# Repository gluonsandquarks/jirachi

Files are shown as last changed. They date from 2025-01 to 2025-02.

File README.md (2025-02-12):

# Jirachi: self-balancing Reuleaux triangle

Jirachi is an embedded device in the shape of a Reuleaux triangle which is able to balance itself in the positions where the system is unstable. This is done through active control in the form of a PID controller.

> [!NOTE]
> This project is still active and being worked on, the firmware for the device and the software for the control GUI is mostly done, the hardware is completely done (no plan for future revisions), and the mechanical side of the project is currently the main focus, as well as documentation.
>
> UPDATE: The mechanical design is mostly done, just need to perform more tests and tune the PID controller again for this new design, after everything's done I'll update the documentation with a nice gif and pictures :)

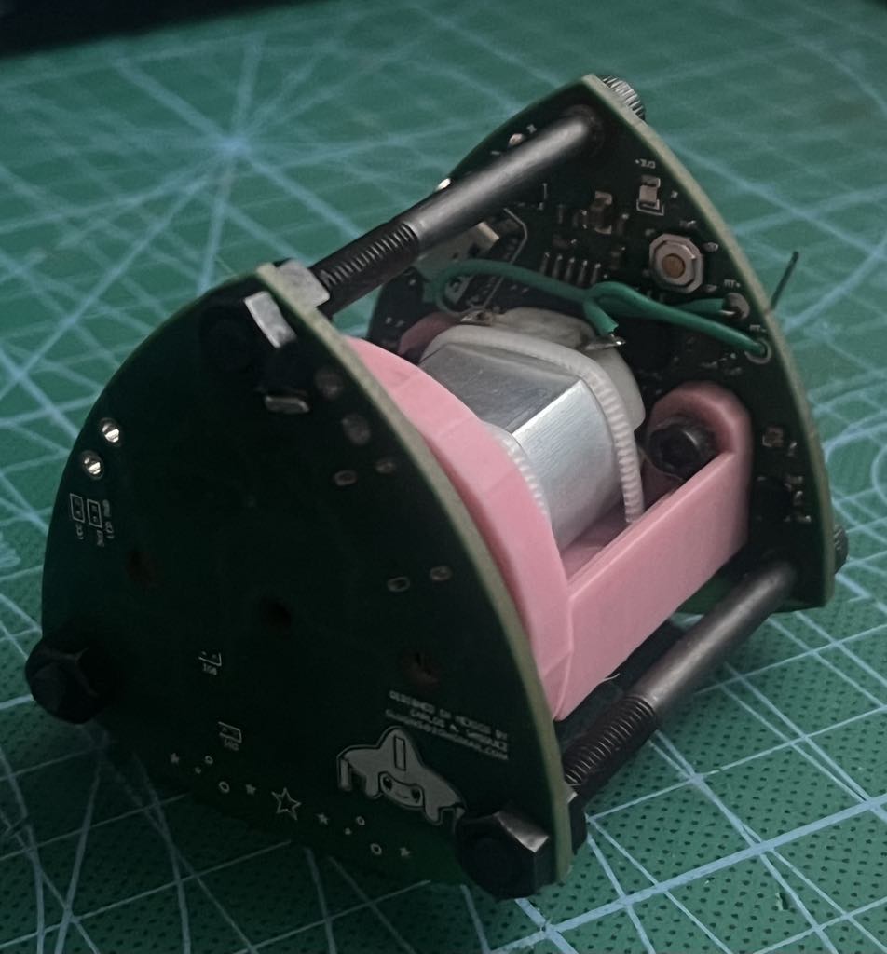
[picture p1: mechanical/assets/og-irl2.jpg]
Jirachi Device


This repository keeps track of all the work that's needed to be done in order to create a product from scratch. The solutions provided aren't necessarily the best ones out there, but the ones that made sense to me as a solo developer given the nature of the project (which is a personal project if it wasn't obvious).

## Overview

As you would be able to tell from the four directories at the root of the repository, each of them aims to solve a specific problem that would ultimately solve the "i want a balancing-robot-thingy" issue. Here's an brief explanation of each folder in the same chronology as this was being developed:

- `hardware/`: This folder holds all the files related to the electronics of the device. This is essentially the device itself and the schematic design and PCB layout was done on Altium Designer. You will be able to find each of the schematics, the PCB project, and the outputs generated by the program to manufacture and assemble the PCB. There are other miscellaneous files used by the program to correctly understand the relation between the mechanical constrains of the device and the actual electronics design needed to be done. [You can read more about this section over here.](hardware/README.md)
- `mechanical/`: This folder holds all the files and data related to the mechanical design of the device. This means any part that is not the PCB itself or soldered directly to it. Technically this aspect of the device was being developed alongside the hardware, as I was jumping back and forth between programs so I could generate mechanical data to add to the hardware program, and viceversa so I could generate a plausible assembly from the PCB data. The mechanical design was worked on CATIA V5, the most interesting thing is the Reuleaux triangle, although it is pretty trivial to implement. Other than that, here is where I defined the assembly, the shape of the motor mount, the flywheel, enclosure, etc. [You can read more about this section over here.](mechanical/README.md)
- `fimrware/`: This folder holds all the source code running on the device. The code implements the RGB LED controller, intertial measurement unit driver, motor driver, Bluetooth Low Energy driver, the PID controller and the sensor-fusion algorithm. The source code is written in C, using the ESP-IDF framework. [You can read more about this section over here.](firmware/README.md)
- `gui/`: This folder holds the source code of a GUI application used to tune the PID controller and enable the control algorithm over BLE. It's implemented in Rust just because I wanted to learn it in a more complex project hehe. It is supposed to be cross-platform but I've just tested on Windows cause my linux distro on my dual booted machine is broken at the moment so whatever (i would just use linux only but i wanted to use some specific CAD programs, so cry about it :P). [You can read more about this section over here.](gui/README.md) ALSO!!! the only reason i created a GUI app to control the device was because stupid windows couldn't connect to my device without pairing first, and to do the pairing i need to define some super specific bloated BLE characteristics so whatever i just did my own solution >:))). You can read more about that particular issue [over here.](https://github.com/espressif/esp-idf/issues/10653#issuecomment-1751914245)

## Build one yourself!!! (Bill of Materials)

If, by some weird reason, you want to build this device from scratch, then let me tell you i would love to see pictures of this lol. Send 'em my way!!! Here's a high level overview of what you'd need to build this device:

- 1 x Assembled PCB: you can just order it from JLCPCB at a pretty cheap price (~20 usd per board), everything is already done for you over at the hardware directory!!
- 1 x DC motor: I used [this one](https://www.amazon.com/dp/B07JYM8H18)
- 1 x Motor coupler: I used [this one](https://www.amazon.com/dp/B0BZS347G5)
- 1 x 3D prints of the models under the [`mechanical/outputs/`](mechanical/outputs/) folder
- 3 x M4x50mm screws
- 6 x M4 nuts
- 2 x M3x10mm screws
- 2 x M3 nuts
- 1 x Li-Ion/LiPo Battery (can be any kind as long as voltage is between 5 and 3.6V, an it can deliver ~1.5A). I used a 18650 cell with a capacity of 2600 mAh
- 2 x zip ties ~2 or 3 mm in width
- 1 x sick soldering and assembly skillz

## Repository Structure
```
├───firmware   -> actual code running on the embedded device
│   ├───docs   -> extra documentation regarding algorithms
│   ├───main   -> source code, built with the esp-idf framework
│   └───tests
├───gui        -> cross-platform gui to connect and control the device
│   ├───assets -> images used by the gui README.md
│   └───src    -> rust source code
├───hardware   -> altium designer files with the schematics and PCB
│   ├───assets -> images used by the hardware README.md
│   ├───libraries -> component libraries
│   │   ├───Phil's Lab
│   │   └───Terreneitor
│   └───Project Outputs for Lucido -> gerbers, BOM and CPL files for manufactury/assembly of the boards
└───mechanical -> 3D models/designs for everything else, done in CATIA
    └───assets -> images used by the mechanical README.md
```

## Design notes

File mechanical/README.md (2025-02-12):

# Jirachi Mechanical Design
The mechanical design for the Jirachi device encloses the PCB in such a way that it extends the shape of the PCB, modifying its mechanical properties so that the control of the device is more stable.

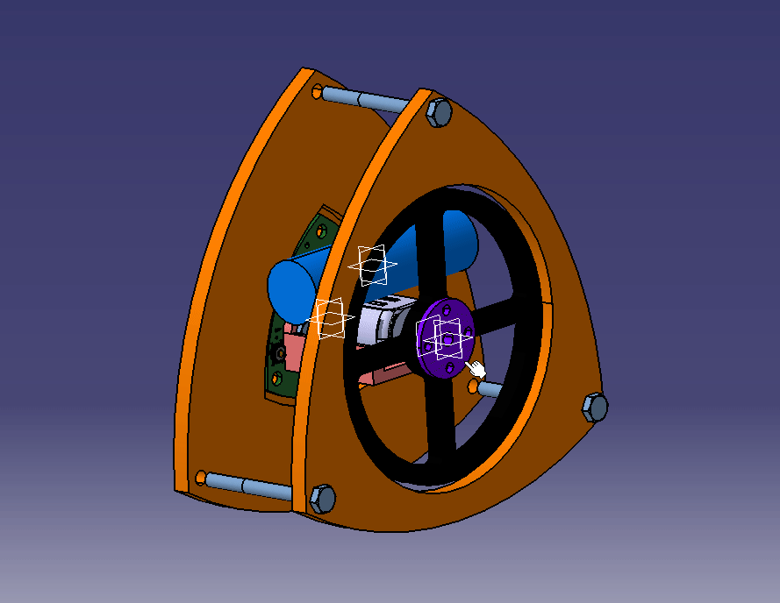
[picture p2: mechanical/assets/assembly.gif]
Assembly


The flywheel is embedded into the device and cuts some of the front plate, this is to both minimize the weight of the device as a whole and because it looks cool lol. The only thing missing is a battery holder, but i got lazy and decided to duct tape the battery on top of the motor or below the motor base (the latter sounds more secure so yeah).

The filenames of of the CATIA models are all fucked because CATIA sucks at renaming the actual archives, the links and everything will break if you try to do that so I'm just avoiding it hehe. If you open the main file `ASSYFinal.CATProduct` you will find the tree and everything should be properly named with names that actually make sense.

At the moment I still need to take pictures of the IRL assembly, but the design as a whole might be done for good.

## Original Design
The original design was implemented by trying to have the PCBs themselves be the mechanical feature that was in constant control. The following gif visualizes the original concept:

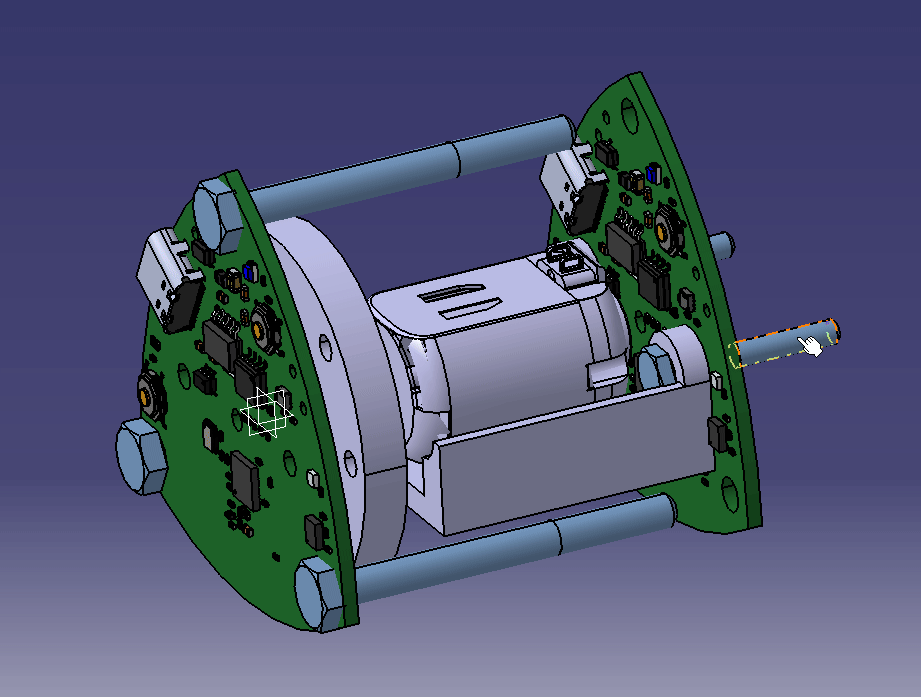
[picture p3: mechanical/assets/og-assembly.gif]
Original Assembly


As you can see, the idea was to have a PCB on one side and another on the other side, sandwiching the motor and the flywheel for the active controller to change the angular momentum of the device in such a way that it could balance itself in one of the three unstable points of the shape (the 3 vertices of the triangle). This ideally works, however after testing and after trying to tune the PID controller, it was noted that the system was really unstable due to the distribution of the moments of intertia, mass, etc.

This is analog to trying to balance a pencil in the tip of your fingers vs. trying to balance a broom in the palm of your hand. The pencil requires a way more responsive controller than the broom. In fact due to how the moments of intertia and mass are distributed on the broom, it is really easy to balance it with minimal input from your hand.

Here are some pics from the original assembly!!
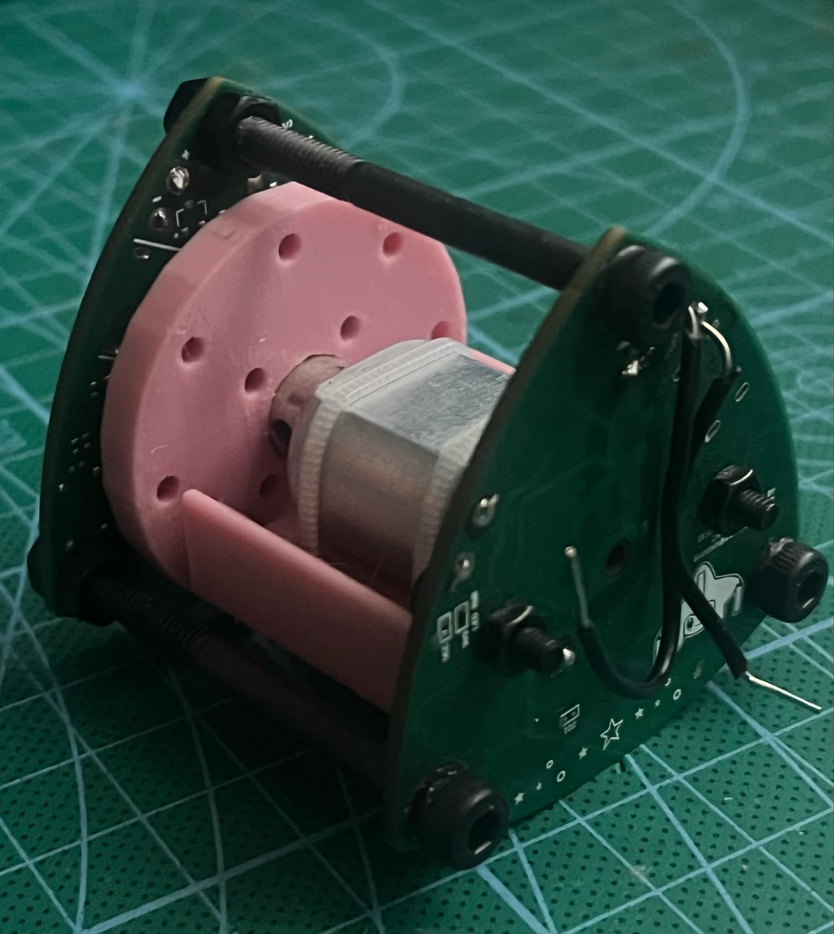
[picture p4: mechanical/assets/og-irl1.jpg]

IRL assembly

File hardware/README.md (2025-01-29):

# Jirachi Hardware

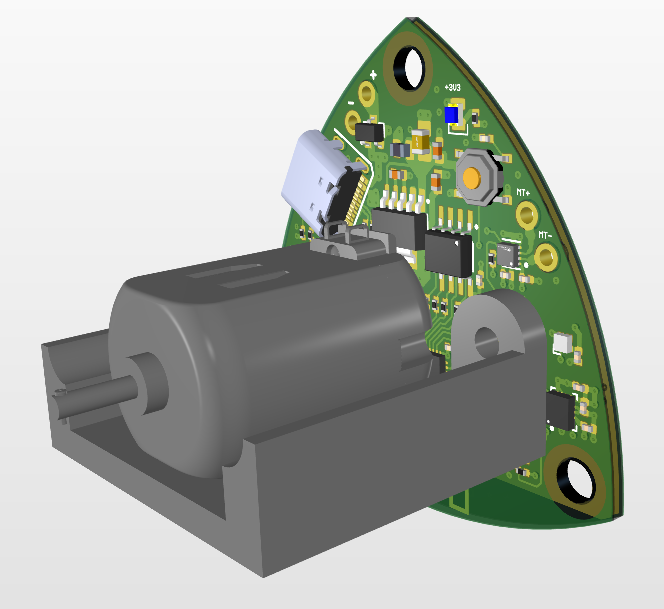
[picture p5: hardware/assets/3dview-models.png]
PCB Isometric View


The hardware for the Jirachi device is a custom designed PCB in the shape of a Reuleaux triangle. The original idea behind this design choice was to have two sets of PCBs sandwich an actuator, this way the PCB itself was designed to be the enclosure itself. Long story short, this original design didn't work [and you can read more about it over here.](../mechanical/README.md#original-design) Over all the mechanical features of the PCB didn't interfere with functionality so it stayed as it was originally planned.

The project was called `Lucido` before I decided to call it `Jirachi`, so that's why the hardware files have different filenames instead of the repository's name.

## Techincal Details

The PCB is a 4-layer board in the shape of a Reuleaux triangle. This special shape is known as a constant-width solid. The maximum width of the PCB is 50mm (you already know this size was intentional due to the discount over at JLCPCB for 4-layer boards nyehehehe, i'm poor like that :P). Here's the breakdown:

- 4-layer PCB: top and bottom layers used for signal and power routing, inner layers used exclusively as ground planes for optimal EMI and EMC.
- 50 mm max width.
- [ESP32-C3](https://www.espressif.com/sites/default/files/documentation/esp32-c3_datasheet_en.pdf): pretty cheap and powerful, able to run control algorithms smoothly, controlled through Bluetooh Low Energy.
- USB-C: This board uses the native USB/JTAG controller to program, debug and power the device. There's no fancy USB-C power delivery or anything like that, but I prefer using it over the more traditional type B and A because the current limit is a little higher ~1A.
- [W25Q128JVSIQ](https://www.winbond.com/resource-files/w25q128jv%20revf%2003272018%20plus.pdf) 128Mbit QSPI Flash.
- [TPS73733DCQR](https://www.ti.com/lit/ds/symlink/tps737.pdf) 1A low-dropout voltage regulator: this thing is a beauty thanks to the super low-dropout voltage and the max current draw available. With this IC, it was a no-brainer having the board being powered by USB or by an external single cell lithium battery.
- [ICM-42688-P](https://product.tdk.com/system/files/dam/doc/product/sensor/mortion-inertial/imu/data_sheet/ds-000347-icm-42688-p-v1.6.pdf) intertial measurment unit: it has a 3-axis accelerometer and a 3-axis gyroscope, with this it is possible to implement attitude estimation through a sensor-fusion algorithm.
- [SK6805-EC15](https://cdn-shop.adafruit.com/product-files/4492/Datasheet.pdf): you already know we need some RGB in this mf. It's just a single RGB LED onboard, but it does more than enough to signal the different states of the device.
- [DRV8837DSGR](https://www.ti.com/lit/ds/symlink/drv8838.pdf?ts=1737923637450): motor driver up to 1.8 A!! It's crazy how this IC being so small can handle almost 2 A. It's controller through two independent PWM channels and the motor is connected directly to the board's main input power source.
- Embedded PCB antenna: implemented from this [TI's Application Note](https://www.ti.com/lit/an/swra117d/swra117d.pdf). This antenna is designed to be resonant @ 2.4 GHz, used for the BLE (and maybe also Wi-Fi if i'm not too lazy) connectivity.

## Ordering the device

The gerber files are available inside the `Project Outputs for Lucido` directory. You can just drop the `LUCIDO_GERBER.zip` file into your favorite PCB manufacturer website. The `LUCIDO_BOM.csv` and `LUCIDO_CPL.csv` are the BOM and component placement files respectively, but they are tailored to work with JLCPCB's assembly service specifically.

## Detailed BOM

Bill of Materials

## Pretty Pictures

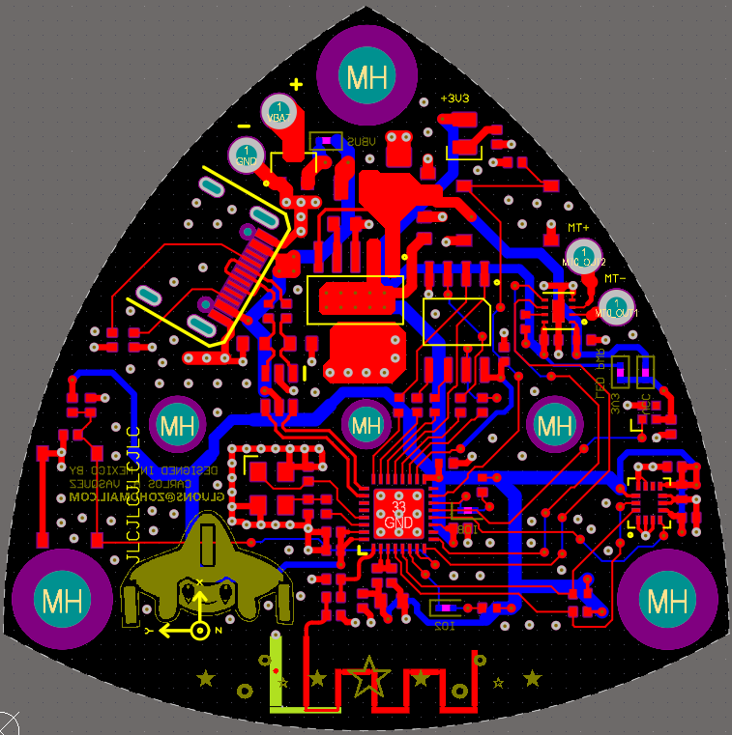
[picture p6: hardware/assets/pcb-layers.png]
PCB top and bottom layers

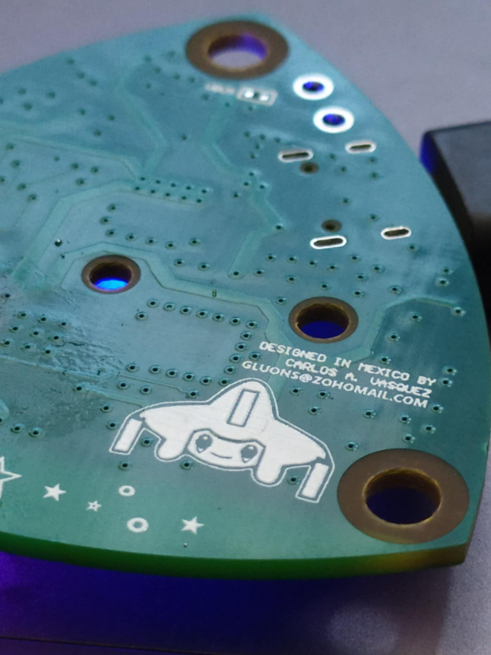
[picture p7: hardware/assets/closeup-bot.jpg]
Close up bottom

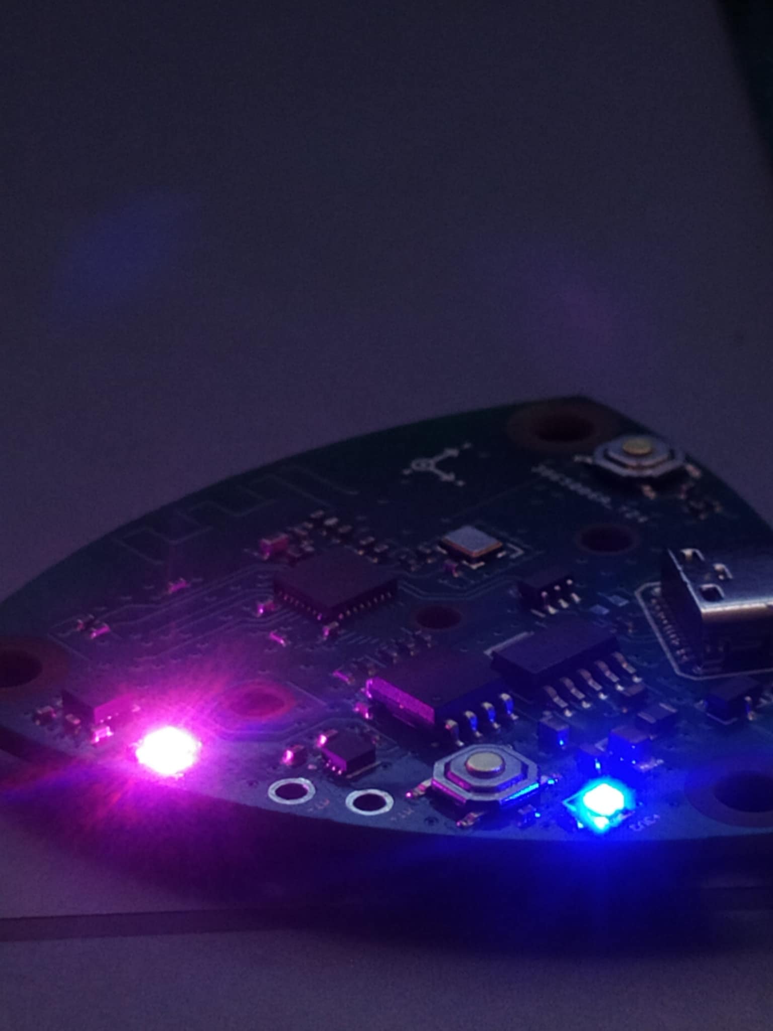
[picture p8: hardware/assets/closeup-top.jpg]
Close up top

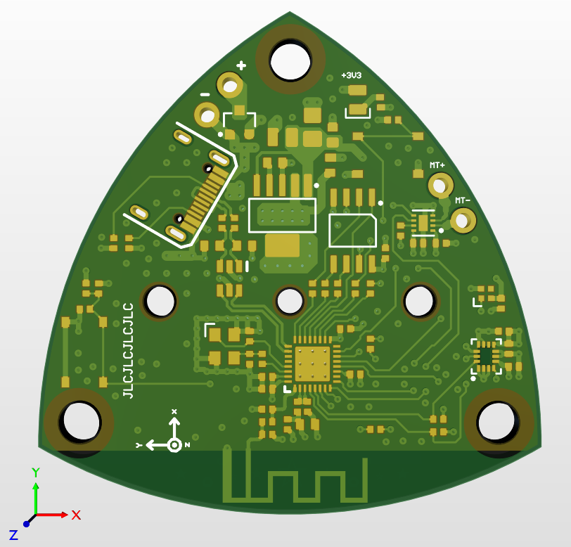
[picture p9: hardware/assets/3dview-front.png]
3D Front

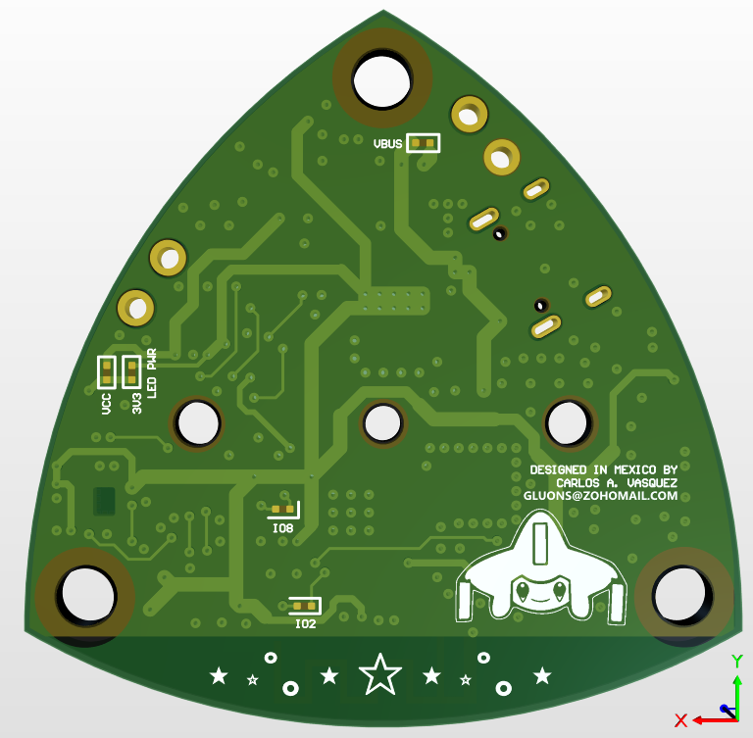
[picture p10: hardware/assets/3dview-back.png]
3D Back


## Known Issues
- NONE this is a perfect PCB!!!
- Forgot to add vias underneath the motor driver IC lol. I have other designs with this same IC that do have them, I just did this in one night and totally forgot to add this thermal via lmfao. It doesn't overheat really thanks to the huge copper mass in L2 and L3, but the thermals could be better for this board revision...

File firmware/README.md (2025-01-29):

# Jirachi Firmware

This is the source code for the Jirachi device. It is completely written in C under the [ESP-IDF](https://github.com/espressif/esp-idf) framework.

## Quick Start
> [!NOTE]
> Make sure to have ESP-IDF v5.3.1 or higher installed and configured.
```
$ idf.py set-target esp32c3
$ idf.py build
```
You can upload the binary to your ESP32-C3 device with
```
$ idf.py -p <PORT> flash
```

## Overview
The firmware implements the following:

- I2C driver to completely communicate with and manage the onboard Inertial Measurement Unit (IMU - accelerometer and gyroscope).
- Bluetooth Low Energy driver and event handler running on a separate thread for wireless control and tuning of the PID controller.
- Madgwick Filter sensor-fusion algorithm implementation. Takes reading from the IMU and estimate the device's current attitude.
- A PID controller implementation.
- Motor driver with independent PWM channels, all exposed through a simple API.
- RGB LED driver implemented with the RMT peripheral for precise control, all exposed through a simple API. It also implements a manager for color blending and custom light show sequences.
- Runs on Espressif's fork of FreeRTOS.

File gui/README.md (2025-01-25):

# Jirachi GUI

The Jirachi GUI is a cross-platform GUI made in Rust to control and tune the PID controller inside of the jirachi device. It is written around the [iced GUI framework](https://github.com/iced-rs/iced) and the [btleplug library](https://github.com/deviceplug/btleplug/tree/master) to easily control the jirachi device and let the GUI app handle all the BLE communication.

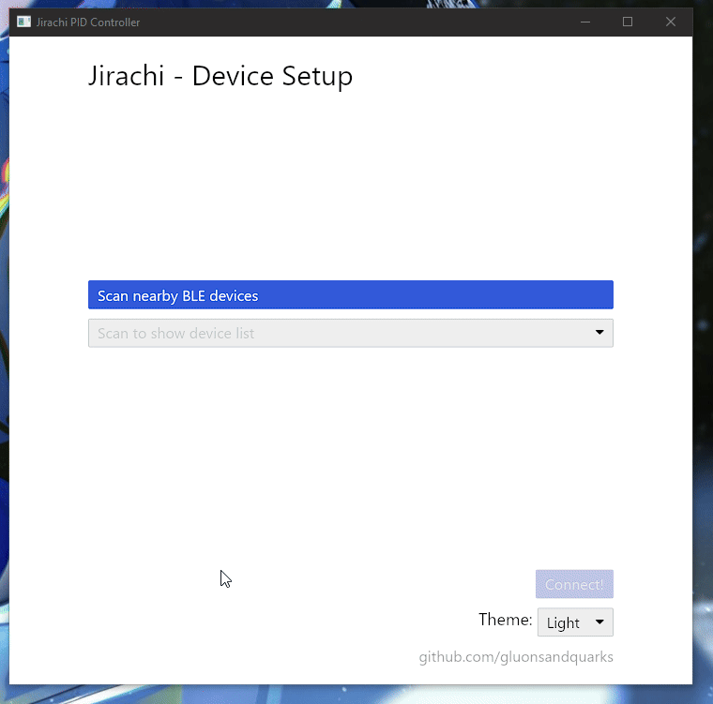
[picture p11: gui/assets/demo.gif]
Demo


## Quick Start

```bash
$ cargo run --release
```

Please don't scream at me for the ugly code, there's only so much I can do with the way the framework works and honestly I'm done with refactoring cause Rust being Rust it is a pain to do rewrite some stuff...

## Dependencies

This project has the following dependencies

```
[dependencies]
btleplug = "0.11.7"
iced = "0.13.1"
uuid = "1.12.1"
```

Turns out that adding a cross-platform GUI and a cross-platform BLE library really bloat your application lmfao but it is what it is and I just wanted a way to circumvent the fact that I needed to define some particular BLE characteristics on my BLE peripheral to be able to connect it and pair it natively to Windows (cause Windows sucks!!!!). You can read more about this issue [over here](https://github.com/espressif/esp-idf/issues/10653#issuecomment-1751914245), a lot of these characteristics weren't needed by my device and honestly is just bloat. Sure I could've implemented them in about 30 mins but where's the fun in that? Instead I spent ~a week developing a GUI that let's me get away with this :P

A side effect of this is that the dependency tree is now fucked lol. oh well, you win some you lose some :)

<details>
<summary>Click to expand huge tree</summary>

```
$ cargo tree
gui v0.1.0 (C:\Users\Usuario\Repos\jirachi\gui)
├── btleplug v0.11.7
│   ├── async-trait v0.1.85 (proc-macro)
│   │   ├── proc-macro2 v1.0.93
│   │   │   └── unicode-ident v1.0.14
│   │   ├── quote v1.0.38
│   │   │   └── proc-macro2 v1.0.93 (*)
│   │   └── syn v2.0.96
│   │       ├── proc-macro2 v1.0.93 (*)
│   │       ├── quote v1.0.38 (*)
│   │       └── unicode-ident v1.0.14
│   ├── bitflags v2.7.0
│   ├── dashmap v6.1.0
│   │   ├── cfg-if v1.0.0
│   │   ├── crossbeam-utils v0.8.21
│   │   ├── hashbrown v0.14.5
│   │   │   ├── ahash v0.8.11
│   │   │   │   ├── cfg-if v1.0.0
│   │   │   │   ├── once_cell v1.20.2
│   │   │   │   └── zerocopy v0.7.35
│   │   │   │   [build-dependencies]
│   │   │   │   └── version_check v0.9.5
│   │   │   └── allocator-api2 v0.2.21
│   │   ├── lock_api v0.4.12
│   │   │   └── scopeguard v1.2.0
│   │   │   [build-dependencies]
│   │   │   └── autocfg v1.4.0
│   │   ├── once_cell v1.20.2
│   │   └── parking_lot_core v0.9.10
│   │       ├── cfg-if v1.0.0
│   │       ├── smallvec v1.13.2
│   │       └── windows-targets v0.52.6
│   │           └── windows_x86_64_msvc v0.52.6
│   ├── futures v0.3.31
│   │   ├── futures-channel v0.3.31
│   │   │   ├── futures-core v0.3.31
│   │   │   └── futures-sink v0.3.31
│   │   ├── futures-core v0.3.31
│   │   ├── futures-executor v0.3.31
│   │   │   ├── futures-core v0.3.31
│   │   │   ├── futures-task v0.3.31
│   │   │   ├── futures-util v0.3.31
│   │   │   │   ├── futures-channel v0.3.31 (*)
│   │   │   │   ├── futures-core v0.3.31
│   │   │   │   ├── futures-io v0.3.31
│   │   │   │   ├── futures-macro v0.3.31 (proc-macro)
│   │   │   │   │   ├── proc-macro2 v1.0.93 (*)
│   │   │   │   │   ├── quote v1.0.38 (*)
│   │   │   │   │   └── syn v2.0.96 (*)
│   │   │   │   ├── futures-sink v0.3.31
│   │   │   │   ├── futures-task v0.3.31
│   │   │   │   ├── memchr v2.7.4
│   │   │   │   ├── pin-project-lite v0.2.16
│   │   │   │   ├── pin-utils v0.1.0
│   │   │   │   └── slab v0.4.9
│   │   │   │       [build-dependencies]
│   │   │   │       └── autocfg v1.4.0
│   │   │   └── num_cpus v1.16.0
│   │   ├── futures-io v0.3.31
│   │   ├── futures-sink v0.3.31
│   │   ├── futures-task v0.3.31
│   │   └── futures-util v0.3.31 (*)
│   ├── log v0.4.25
│   ├── static_assertions v1.1.0
│   ├── thiserror v2.0.11
│   │   └── thiserror-impl v2.0.11 (proc-macro)
│   │       ├── proc-macro2 v1.0.93 (*)
│   │       ├── quote v1.0.38 (*)
│   │       └── syn v2.0.96 (*)
│   ├── tokio v1.43.0
│   │   └── pin-project-lite v0.2.16
│   ├── tokio-stream v0.1.17
│   │   ├── futures-core v0.3.31
│   │   ├── pin-project-lite v0.2.16
│   │   ├── tokio v1.43.0 (*)
│   │   └── tokio-util v0.7.13
│   │       ├── bytes v1.9.0
│   │       ├── futures-core v0.3.31
│   │       ├── futures-sink v0.3.31
│   │       ├── pin-project-lite v0.2.16
│   │       └── tokio v1.43.0 (*)
│   ├── uuid v1.12.1
│   └── windows v0.57.0
│       ├── windows-core v0.57.0
│       │   ├── windows-implement v0.57.0 (proc-macro)
│       │   │   ├── proc-macro2 v1.0.93 (*)
│       │   │   ├── quote v1.0.38 (*)
│       │   │   └── syn v2.0.96 (*)
│       │   ├── windows-interface v0.57.0 (proc-macro)
│       │   │   ├── proc-macro2 v1.0.93 (*)
│       │   │   ├── quote v1.0.38 (*)
│       │   │   └── syn v2.0.96 (*)
│       │   ├── windows-result v0.1.2
│       │   │   └── windows-targets v0.52.6 (*)
│       │   └── windows-targets v0.52.6 (*)
│       └── windows-targets v0.52.6 (*)
├── iced v0.13.1
│   ├── iced_core v0.13.2
│   │   ├── bitflags v2.7.0
│   │   ├── bytes v1.9.0
│   │   ├── dark-light v1.1.1
│   │   │   └── winreg v0.10.1
│   │   │       └── winapi v0.3.9
│   │   ├── glam v0.25.0
│   │   ├── log v0.4.25
│   │   ├── num-traits v0.2.19
│   │   │   [build-dependencies]
│   │   │   └── autocfg v1.4.0
│   │   ├── once_cell v1.20.2
│   │   ├── palette v0.7.6
│   │   │   ├── approx v0.5.1
│   │   │   │   └── num-traits v0.2.19 (*)
│   │   │   ├── fast-srgb8 v1.0.0
│   │   │   ├── palette_derive v0.7.6 (proc-macro)
│   │   │   │   ├── by_address v1.2.1
│   │   │   │   ├── proc-macro2 v1.0.93 (*)
│   │   │   │   ├── quote v1.0.38 (*)
│   │   │   │   └── syn v2.0.96 (*)
│   │   │   └── phf v0.11.3
│   │   │       ├── phf_macros v0.11.3 (proc-macro)
│   │   │       │   ├── phf_generator v0.11.3
│   │   │       │   │   ├── phf_shared v0.11.3
│   │   │       │   │   │   └── siphasher v1.0.1
│   │   │       │   │   └── rand v0.8.5
│   │   │       │   │       └── rand_core v0.6.4
│   │   │       │   ├── phf_shared v0.11.3 (*)
│   │   │       │   ├── proc-macro2 v1.0.93 (*)
│   │   │       │   ├── quote v1.0.38 (*)
│   │   │       │   └── syn v2.0.96 (*)
│   │   │       └── phf_shared v0.11.3 (*)
│   │   ├── rustc-hash v2.1.0
│   │   ├── smol_str v0.2.2
│   │   ├── thiserror v1.0.69
│   │   │   └── thiserror-impl v1.0.69 (proc-macro)
│   │   │       ├── proc-macro2 v1.0.93 (*)
│   │   │       ├── quote v1.0.38 (*)
│   │   │       └── syn v2.0.96 (*)
│   │   └── web-time v1.1.0
│   ├── iced_futures v0.13.2
│   │   ├── futures v0.3.31 (*)
│   │   ├── iced_core v0.13.2 (*)
│   │   ├── log v0.4.25
│   │   └── rustc-hash v2.1.0
│   ├── iced_renderer v0.13.0
│   │   ├── iced_graphics v0.13.0
│   │   │   ├── bitflags v2.7.0
│   │   │   ├── bytemuck v1.21.0
│   │   │   │   └── bytemuck_derive v1.8.1 (proc-macro)
│   │   │   │       ├── proc-macro2 v1.0.93 (*)
│   │   │   │       ├── quote v1.0.38 (*)
│   │   │   │       └── syn v2.0.96 (*)
│   │   │   ├── cosmic-text v0.12.1
│   │   │   │   ├── bitflags v2.7.0
│   │   │   │   ├── fontdb v0.16.2
│   │   │   │   │   ├── log v0.4.25
│   │   │   │   │   ├── memmap2 v0.9.5
│   │   │   │   │   ├── slotmap v1.0.7
│   │   │   │   │   │   [build-dependencies]
│   │   │   │   │   │   └── version_check v0.9.5
│   │   │   │   │   ├── tinyvec v1.8.1
│   │   │   │   │   │   └── tinyvec_macros v0.1.1
│   │   │   │   │   └── ttf-parser v0.20.0
│   │   │   │   ├── log v0.4.25
│   │   │   │   ├── rangemap v1.5.1
│   │   │   │   ├── rayon v1.10.0
│   │   │   │   │   ├── either v1.13.0
│   │   │   │   │   └── rayon-core v1.12.1
│   │   │   │   │       ├── crossbeam-deque v0.8.6
│   │   │   │   │       │   ├── crossbeam-epoch v0.9.18
│   │   │   │   │       │   │   └── crossbeam-utils v0.8.21
│   │   │   │   │       │   └── crossbeam-utils v0.8.21
│   │   │   │   │       └── crossbeam-utils v0.8.21
│   │   │   │   ├── rustc-hash v1.1.0
│   │   │   │   ├── rustybuzz v0.14.1
│   │   │   │   │   ├── bitflags v2.7.0
│   │   │   │   │   ├── bytemuck v1.21.0 (*)
│   │   │   │   │   ├── libm v0.2.11
│   │   │   │   │   ├── smallvec v1.13.2
│   │   │   │   │   ├── ttf-parser v0.21.1
│   │   │   │   │   ├── unicode-bidi-mirroring v0.2.0
│   │   │   │   │   ├── unicode-ccc v0.2.0
│   │   │   │   │   ├── unicode-properties v0.1.3
│   │   │   │   │   └── unicode-script v0.5.7
│   │   │   │   ├── self_cell v1.1.0
│   │   │   │   ├── swash v0.1.19
│   │   │   │   │   ├── skrifa v0.22.3
│   │   │   │   │   │   ├── bytemuck v1.21.0 (*)
│   │   │   │   │   │   └── read-fonts v0.22.7
│   │   │   │   │   │       ├── bytemuck v1.21.0 (*)
│   │   │   │   │   │       └── font-types v0.7.3
│   │   │   │   │   │           └── bytemuck v1.21.0 (*)
│   │   │   │   │   ├── yazi v0.1.6
│   │   │   │   │   └── zeno v0.2.3
│   │   │   │   ├── sys-locale v0.3.2
│   │   │   │   ├── ttf-parser v0.21.1
│   │   │   │   ├── unicode-bidi v0.3.18
│   │   │   │   ├── unicode-linebreak v0.1.5
│   │   │   │   ├── unicode-script v0.5.7
│   │   │   │   └── unicode-segmentation v1.12.0
│   │   │   ├── half v2.4.1
│   │   │   │   └── cfg-if v1.0.0
│   │   │   ├── iced_core v0.13.2 (*)
│   │   │   ├── iced_futures v0.13.2 (*)
│   │   │   ├── log v0.4.25
│   │   │   ├── once_cell v1.20.2
│   │   │   ├── raw-window-handle v0.6.2
│   │   │   ├── rustc-hash v2.1.0
│   │   │   ├── thiserror v1.0.69 (*)
│   │   │   └── unicode-segmentation v1.12.0
│   │   ├── iced_tiny_skia v0.13.0
│   │   │   ├── bytemuck v1.21.0 (*)
│   │   │   ├── cosmic-text v0.12.1 (*)
│   │   │   ├── iced_graphics v0.13.0 (*)
│   │   │   ├── kurbo v0.10.4
│   │   │   │   ├── arrayvec v0.7.6
│   │   │   │   └── smallvec v1.13.2
│   │   │   ├── log v0.4.25
│   │   │   ├── rustc-hash v2.1.0
│   │   │   ├── softbuffer v0.4.6
│   │   │   │   ├── log v0.4.25
│   │   │   │   ├── raw-window-handle v0.6.2
│   │   │   │   └── windows-sys v0.59.0
│   │   │   │       └── windows-targets v0.52.6 (*)
│   │   │   │   [build-dependencies]
│   │   │   │   └── cfg_aliases v0.2.1
│   │   │   └── tiny-skia v0.11.4
│   │   │       ├── arrayref v0.3.9
│   │   │       ├── arrayvec v0.7.6
│   │   │       ├── bytemuck v1.21.0 (*)
│   │   │       ├── cfg-if v1.0.0
│   │   │       ├── log v0.4.25
│   │   │       ├── png v0.17.16
│   │   │       │   ├── bitflags v1.3.2
│   │   │       │   ├── crc32fast v1.4.2
│   │   │       │   │   └── cfg-if v1.0.0
│   │   │       │   ├── fdeflate v0.3.7
│   │   │       │   │   └── simd-adler32 v0.3.7
│   │   │       │   ├── flate2 v1.0.35
│   │   │       │   │   ├── crc32fast v1.4.2 (*)
│   │   │       │   │   └── miniz_oxide v0.8.3
│   │   │       │   │       ├── adler2 v2.0.0
│   │   │       │   │       └── simd-adler32 v0.3.7
│   │   │       │   └── miniz_oxide v0.8.3 (*)
│   │   │       └── tiny-skia-path v0.11.4
│   │   │           ├── arrayref v0.3.9
│   │   │           ├── bytemuck v1.21.0 (*)
│   │   │           └── strict-num v0.1.1
│   │   ├── iced_wgpu v0.13.5
│   │   │   ├── bitflags v2.7.0
│   │   │   ├── bytemuck v1.21.0 (*)
│   │   │   ├── futures v0.3.31 (*)
│   │   │   ├── glam v0.25.0
│   │   │   ├── guillotiere v0.6.2
│   │   │   │   ├── euclid v0.22.11
│   │   │   │   │   └── num-traits v0.2.19 (*)
│   │   │   │   └── svg_fmt v0.4.4
│   │   │   ├── iced_glyphon v0.6.0
│   │   │   │   ├── cosmic-text v0.12.1 (*)
│   │   │   │   ├── etagere v0.2.13
│   │   │   │   │   ├── euclid v0.22.11 (*)
│   │   │   │   │   └── svg_fmt v0.4.4
│   │   │   │   ├── lru v0.12.5
│   │   │   │   ├── rustc-hash v2.1.0
│   │   │   │   └── wgpu v0.19.4
│   │   │   │       ├── arrayvec v0.7.6
│   │   │   │       ├── cfg-if v1.0.0
│   │   │   │       ├── log v0.4.25
│   │   │   │       ├── parking_lot v0.12.3
│   │   │   │       │   ├── lock_api v0.4.12 (*)
│   │   │   │       │   └── parking_lot_core v0.9.10 (*)
│   │   │   │       ├── profiling v1.0.16
│   │   │   │       ├── raw-window-handle v0.6.2
│   │   │   │       ├── smallvec v1.13.2
│   │   │   │       ├── static_assertions v1.1.0
│   │   │   │       ├── wgpu-core v0.19.4
│   │   │   │       │   ├── arrayvec v0.7.6
│   │   │   │       │   ├── bit-vec v0.6.3
│   │   │   │       │   ├── bitflags v2.7.0
│   │   │   │       │   ├── codespan-reporting v0.11.1
│   │   │   │       │   │   ├── termcolor v1.4.1
│   │   │   │       │   │   │   └── winapi-util v0.1.9
│   │   │   │       │   │   │       └── windows-sys v0.59.0 (*)
│   │   │   │       │   │   └── unicode-width v0.1.14
│   │   │   │       │   ├── indexmap v2.7.0
│   │   │   │       │   │   ├── equivalent v1.0.1
│   │   │   │       │   │   └── hashbrown v0.15.2
│   │   │   │       │   ├── log v0.4.25
│   │   │   │       │   ├── naga v0.19.2
│   │   │   │       │   │   ├── bit-set v0.5.3
│   │   │   │       │   │   │   └── bit-vec v0.6.3
│   │   │   │       │   │   ├── bitflags v2.7.0
│   │   │   │       │   │   ├── codespan-reporting v0.11.1 (*)
│   │   │   │       │   │   ├── hexf-parse v0.2.1
│   │   │   │       │   │   ├── indexmap v2.7.0 (*)
│   │   │   │       │   │   ├── log v0.4.25
│   │   │   │       │   │   ├── num-traits v0.2.19 (*)
│   │   │   │       │   │   ├── rustc-hash v1.1.0
│   │   │   │       │   │   ├── spirv v0.3.0+sdk-1.3.268.0
│   │   │   │       │   │   │   └── bitflags v2.7.0
│   │   │   │       │   │   ├── termcolor v1.4.1 (*)
│   │   │   │       │   │   ├── thiserror v1.0.69 (*)
│   │   │   │       │   │   └── unicode-xid v0.2.6
│   │   │   │       │   ├── once_cell v1.20.2
│   │   │   │       │   ├── parking_lot v0.12.3 (*)
│   │   │   │       │   ├── profiling v1.0.16
│   │   │   │       │   ├── raw-window-handle v0.6.2
│   │   │   │       │   ├── rustc-hash v1.1.0
│   │   │   │       │   ├── smallvec v1.13.2
│   │   │   │       │   ├── thiserror v1.0.69 (*)
│   │   │   │       │   ├── wgpu-hal v0.19.5
│   │   │   │       │   │   ├── arrayvec v0.7.6
│   │   │   │       │   │   ├── ash v0.37.3+1.3.251
│   │   │   │       │   │   │   └── libloading v0.7.4
│   │   │   │       │   │   │       └── winapi v0.3.9
│   │   │   │       │   │   ├── bit-set v0.5.3 (*)
│   │   │   │       │   │   ├── bitflags v2.7.0
│   │   │   │       │   │   ├── d3d12 v0.19.0
│   │   │   │       │   │   │   ├── bitflags v2.7.0
│   │   │   │       │   │   │   ├── libloading v0.8.6
│   │   │   │       │   │   │   │   └── windows-targets v0.52.6 (*)
│   │   │   │       │   │   │   └── winapi v0.3.9
│   │   │   │       │   │   ├── glow v0.13.1
│   │   │   │       │   │   ├── glutin_wgl_sys v0.5.0
│   │   │   │       │   │   │   [build-dependencies]
│   │   │   │       │   │   │   └── gl_generator v0.14.0
│   │   │   │       │   │   │       ├── khronos_api v3.1.0
│   │   │   │       │   │   │       ├── log v0.4.25
│   │   │   │       │   │   │       └── xml-rs v0.8.25
│   │   │   │       │   │   ├── gpu-alloc v0.6.0
│   │   │   │       │   │   │   ├── bitflags v2.7.0
│   │   │   │       │   │   │   └── gpu-alloc-types v0.3.0
│   │   │   │       │   │   │       └── bitflags v2.7.0
│   │   │   │       │   │   ├── gpu-allocator v0.25.0
│   │   │   │       │   │   │   ├── log v0.4.25
│   │   │   │       │   │   │   ├── presser v0.3.1
│   │   │   │       │   │   │   ├── thiserror v1.0.69 (*)
│   │   │   │       │   │   │   ├── winapi v0.3.9
│   │   │   │       │   │   │   └── windows v0.52.0
│   │   │   │       │   │   │       ├── windows-core v0.52.0
│   │   │   │       │   │   │       │   └── windows-targets v0.52.6 (*)
│   │   │   │       │   │   │       └── windows-targets v0.52.6 (*)
│   │   │   │       │   │   ├── gpu-descriptor v0.2.4
│   │   │   │       │   │   │   ├── bitflags v2.7.0
│   │   │   │       │   │   │   ├── gpu-descriptor-types v0.1.2
│   │   │   │       │   │   │   │   └── bitflags v2.7.0
│   │   │   │       │   │   │   └── hashbrown v0.14.5 (*)
│   │   │   │       │   │   ├── hassle-rs v0.11.0
│   │   │   │       │   │   │   ├── bitflags v2.7.0
│   │   │   │       │   │   │   ├── com v0.6.0
│   │   │   │       │   │   │   │   └── com_macros v0.6.0 (proc-macro)
│   │   │   │       │   │   │   │       ├── com_macros_support v0.6.0
│   │   │   │       │   │   │   │       │   ├── proc-macro2 v1.0.93 (*)
│   │   │   │       │   │   │   │       │   ├── quote v1.0.38 (*)
│   │   │   │       │   │   │   │       │   └── syn v1.0.109
│   │   │   │       │   │   │   │       │       ├── proc-macro2 v1.0.93 (*)
│   │   │   │       │   │   │   │       │       ├── quote v1.0.38 (*)
│   │   │   │       │   │   │   │       │       └── unicode-ident v1.0.14
│   │   │   │       │   │   │   │       ├── proc-macro2 v1.0.93 (*)
│   │   │   │       │   │   │   │       └── syn v1.0.109 (*)
│   │   │   │       │   │   │   ├── libloading v0.8.6 (*)
│   │   │   │       │   │   │   ├── thiserror v1.0.69 (*)
│   │   │   │       │   │   │   ├── widestring v1.1.0
│   │   │   │       │   │   │   └── winapi v0.3.9
│   │   │   │       │   │   ├── khronos-egl v6.0.0
│   │   │   │       │   │   │   ├── libc v0.2.169
│   │   │   │       │   │   │   └── libloading v0.8.6 (*)
│   │   │   │       │   │   ├── libloading v0.8.6 (*)
│   │   │   │       │   │   ├── log v0.4.25
│   │   │   │       │   │   ├── naga v0.19.2 (*)
│   │   │   │       │   │   ├── once_cell v1.20.2
│   │   │   │       │   │   ├── parking_lot v0.12.3 (*)
│   │   │   │       │   │   ├── profiling v1.0.16
│   │   │   │       │   │   ├── range-alloc v0.1.3
│   │   │   │       │   │   ├── raw-window-handle v0.6.2
│   │   │   │       │   │   ├── renderdoc-sys v1.1.0
│   │   │   │       │   │   ├── rustc-hash v1.1.0
│   │   │   │       │   │   ├── smallvec v1.13.2
│   │   │   │       │   │   ├── thiserror v1.0.69 (*)
│   │   │   │       │   │   ├── wgpu-types v0.19.2
│   │   │   │       │   │   │   └── bitflags v2.7.0
│   │   │   │       │   │   └── winapi v0.3.9
│   │   │   │       │   │   [build-dependencies]
│   │   │   │       │   │   └── cfg_aliases v0.1.1
│   │   │   │       │   └── wgpu-types v0.19.2 (*)
│   │   │   │       │   [build-dependencies]
│   │   │   │       │   └── cfg_aliases v0.1.1
│   │   │   │       ├── wgpu-hal v0.19.5 (*)
│   │   │   │       └── wgpu-types v0.19.2 (*)
│   │   │   │       [build-dependencies]
│   │   │   │       └── cfg_aliases v0.1.1
│   │   │   ├── iced_graphics v0.13.0 (*)
│   │   │   ├── log v0.4.25
│   │   │   ├── once_cell v1.20.2
│   │   │   ├── rustc-hash v2.1.0
│   │   │   ├── thiserror v1.0.69 (*)
│   │   │   └── wgpu v0.19.4 (*)
│   │   ├── log v0.4.25
│   │   └── thiserror v1.0.69 (*)
│   ├── iced_widget v0.13.4
│   │   ├── iced_renderer v0.13.0 (*)
│   │   ├── iced_runtime v0.13.2
│   │   │   ├── bytes v1.9.0
│   │   │   ├── iced_core v0.13.2 (*)
│   │   │   ├── iced_futures v0.13.2 (*)
│   │   │   ├── raw-window-handle v0.6.2
│   │   │   └── thiserror v1.0.69 (*)
│   │   ├── num-traits v0.2.19 (*)
│   │   ├── once_cell v1.20.2
│   │   ├── rustc-hash v2.1.0
│   │   ├── thiserror v1.0.69 (*)
│   │   └── unicode-segmentation v1.12.0
│   ├── iced_winit v0.13.0
│   │   ├── iced_futures v0.13.2 (*)
│   │   ├── iced_graphics v0.13.0 (*)
│   │   ├── iced_runtime v0.13.2 (*)
│   │   ├── log v0.4.25
│   │   ├── rustc-hash v2.1.0
│   │   ├── thiserror v1.0.69 (*)
│   │   ├── tracing v0.1.41
│   │   │   ├── pin-project-lite v0.2.16
│   │   │   ├── tracing-attributes v0.1.28 (proc-macro)
│   │   │   │   ├── proc-macro2 v1.0.93 (*)
│   │   │   │   ├── quote v1.0.38 (*)
│   │   │   │   └── syn v2.0.96 (*)
│   │   │   └── tracing-core v0.1.33
│   │   │       └── once_cell v1.20.2
│   │   ├── winapi v0.3.9
│   │   ├── window_clipboard v0.4.1
│   │   │   ├── clipboard-win v5.4.0
│   │   │   │   └── error-code v3.3.1
│   │   │   ├── raw-window-handle v0.6.2
│   │   │   └── thiserror v1.0.69 (*)
│   │   └── winit v0.30.8
│   │       ├── bitflags v2.7.0
│   │       ├── cursor-icon v1.1.0
│   │       ├── dpi v0.1.1
│   │       ├── raw-window-handle v0.6.2
│   │       ├── smol_str v0.2.2
│   │       ├── tracing v0.1.41 (*)
│   │       ├── unicode-segmentation v1.12.0
│   │       └── windows-sys v0.52.0
│   │           └── windows-targets v0.52.6 (*)
│   │       [build-dependencies]
│   │       └── cfg_aliases v0.2.1
│   └── thiserror v1.0.69 (*)
└── uuid v1.12.1
```

</details>

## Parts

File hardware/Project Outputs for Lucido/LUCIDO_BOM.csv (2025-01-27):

Comment | Description | Designator | Footprint | LibRef | Quantity | LCSC Part #
10u | Capacitor SMD 0805 | C100 | CAP_0805 | CAP_0805 | 1 | C15850
100n | Capacitor SMD 0603 | C101, C102 | CAP_0603 | CAP_0603 | 2 | C14663
22u | Capacitor SMD 0603 | C103 | CAP_0603 | CAP_0603 | 1 | C59461
1u | Capacitor SMD 0402 | C200, C208, C218 | CAP_0402 | CAP_0402 | 3 | C52923
100n | Capacitor SMD 0402 | C201, C202, C203, C204, C207, C211, C216, C217, C300, C400, C401 | CAP_0402 | CAP_0402 | 11 | C1525
10u | Capacitor SMD 0603 | C206 | CAP_0603 | CAP_0603 | 1 | C19702
3p3 | Capacitor SMD 0402 | C209, C210 | CAP_0402 | CAP_0402 | 2 | C1565
10p | Capacitor SMD 0402 | C212, C213 | CAP_0402 | CAP_0402 | 2 | C32949
DNP | Capacitor SMD 0603 | C214, C215 | CAP_0603 | CAP_0603 | 2
10n | Capacitor SMD 0402 | C301 | CAP_0402 | CAP_0402 | 1 | C15195
2u2 | Capacitor SMD 0402 | C302 | CAP_0402 | CAP_0402 | 1 | C12530
BLUE | LED 0805 BLUE SMD | D100 | LED_0805_BLUE | LED_0805_BLUE | 1 | C205441
USBLC6-2SC6 | Low-Capacitance ESD Protection USB | D200 | SOT-23-6 | USBLC6-2SC6 | 1 | C2827654
100R @ 100 MHz | Ferrite Bead SMD 0805 | FB100 | FB_0805 | FB_0805 | 1 | C1015
TYPE-C-31-M-12 | USB Type C Connector Horizontal SMT | J200 | TYPE-C-31-M-12 | TYPE-C-31-M-12 | 1 | C165948
2n2 | Inductor SMD 0402 | L200, L201 | IND_0402 | IND_0402 | 2 | C90191
AO3401A | P-Channel MOSFET, 30 V, 4 A, -55 to 150 degC, 3-Pin SOT-23-3L, RoHS, Tape and Reel | Q100 | AO-SOT-23-3L_V | CMP-2000-05778-1 | 1 | C15127
1k | Resistor SMD 0402 | R100, R400 | RES_0402 | RES_0402 | 2 | C11702
0 | Resistor SMD 0402 | R200, R201, R202, R203, R204, R208, R209 | RES_0402 | RES_0402 | 7 | C17168
22 | Resistor SMD 0402 | R205 | RES_0402 | RES_0402 | 1 | C25092
5k1 | Resistor SMD 0402 | R206, R207, R210, R211, R213, R214 | RES_0402 | RES_0402 | 6 | C25905
10k | Resistor SMD 0402 | R212 | RES_0402 | RES_0402 | 1 | C25744
SW SPST SMD Terreneitor | SPST SW TS-1187A-B-A-B | SW200, SW201 | SW SPST SMD Terreneitor | SW SPST SMD Terreneitor | 2 | C318884
TPS73733DCQR | Single Output LDO, 1 A, Fixed 3.3 V Output, 2.2 to 5.5 V Input, with Reverse Current Protection, 6-pin SOT-223 (DCQ), -40 to 125 degC, Green (RoHS & no Sb/Br) | U100 | DCQ0006A_N | CMP-0395-00300-2 | 1 | C31334
W25Q128JVSIQ | 128M-BIT SERIAL FLASH MEMORY WITH DUAL/QUAD SPI & QPI & DTR SOIC-8 208 MIL | U200 | SOIC8_208 mil | W25Q128JVSIQ | 1 | C97521
ESP32-C3 | Ultra�Low�Power SoC with RISC�V Single�Core CPU Supporting IEEE 802.11b/g/n (2.4 GHz Wi�Fi) and Bluetooth� 5 (LE) | U201 | QFN32-5x5 | ESP32-C3 | 1 | C2838500
SK6805-EC15 |  | U202 | SK6805-EC15 | SK6805-EC15 | 1 | C2890035
ICM-42688-P | 6-axis MEMS IMU (Accelerometer & Gyroscope) | U300 | LGA14 (2.5mm x 3mm) | ICM-42688-P | 1 | C1850418
DRV8837DSGR | IC MOTOR DRIVER PAR 8WSON | U400 | FP-DSG0008A-MFG | CMP-04915-000004-1 | 1 | C39159
40MHz | Crystal SMD 40MHz 10PPM 12pF 3225 | X200 | XTAL_3225 | TSX-3225_24.0000MF15X-AC | 1 | C5186937

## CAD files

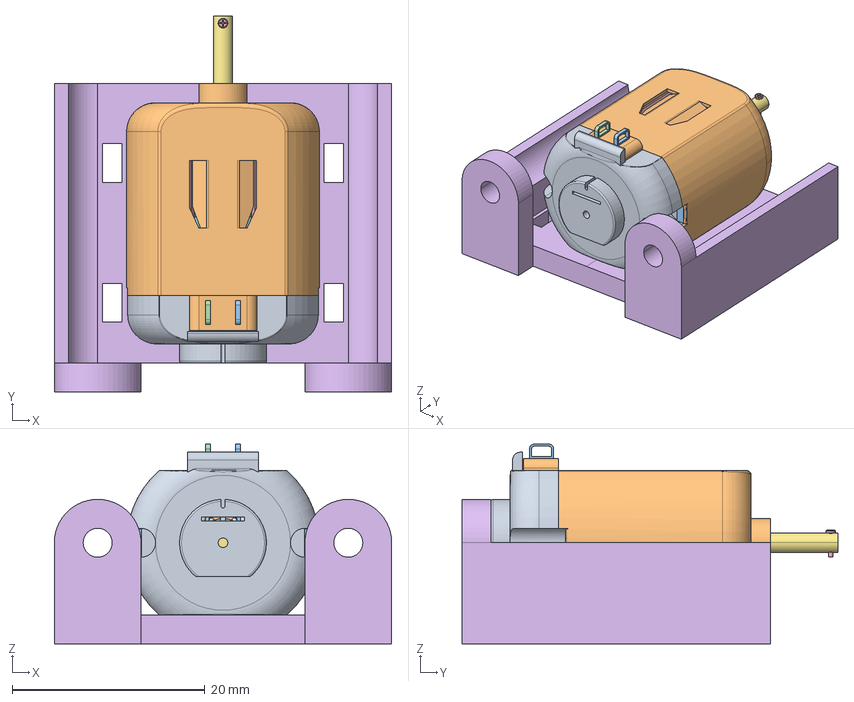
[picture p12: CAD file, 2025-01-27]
hardware/Motor_Assy.stp
35.0 x 39.0 x 20.7 mm

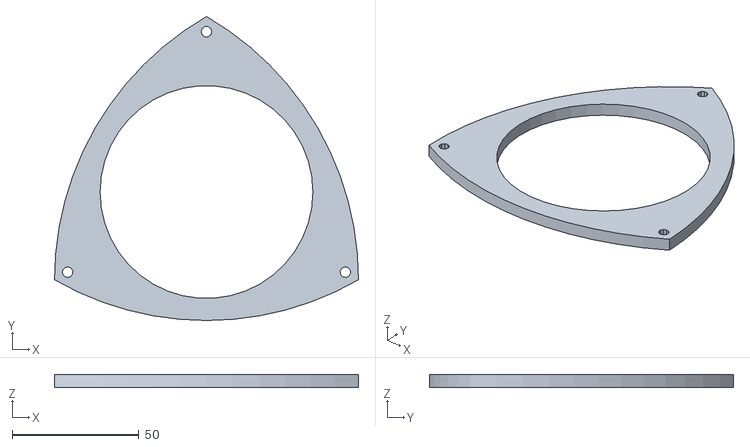
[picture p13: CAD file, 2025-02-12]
mechanical/outputs/front-plate.stl
120.0 x 120.0 x 5.00

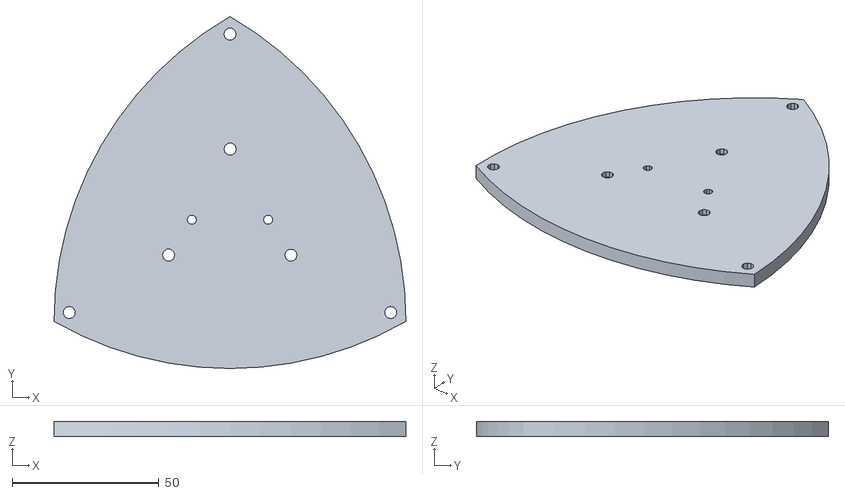
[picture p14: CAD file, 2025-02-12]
mechanical/outputs/back-plate.stl
120.0 x 120.0 x 5.00

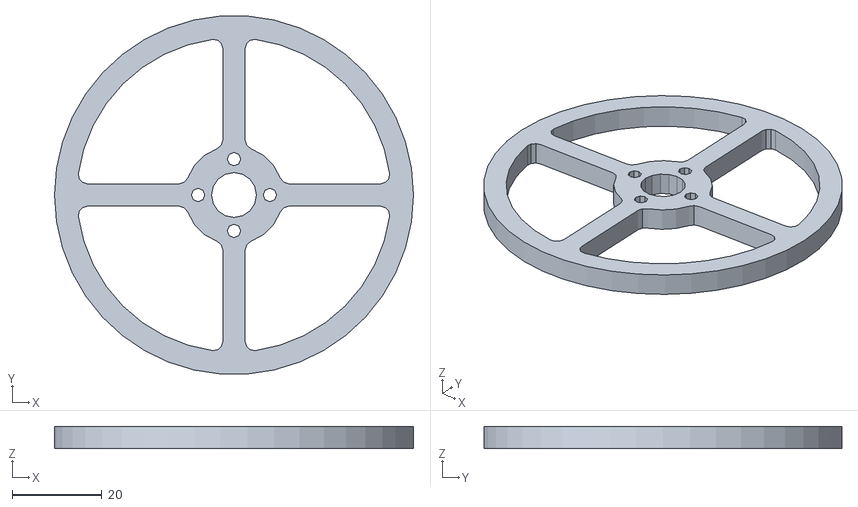
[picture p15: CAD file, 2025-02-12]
mechanical/outputs/flywheel.stl
80.0 x 79.8 x 5.00

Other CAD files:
mechanical/10.CATPart
mechanical/11.CATPart
mechanical/18650.CATPart
mechanical/3.CATPart
mechanical/4.CATPart
mechanical/5.CATPart
mechanical/6.CATPart
mechanical/7.CATPart
mechanical/8.CATPart
mechanical/9.CATPart
mechanical/ASSYFinal.CATProduct
mechanical/Flywheel.CATPart
mechanical/Front Plate.CATPart
mechanical/ISO_4014_M3x20_STEEL_GRADE_A_HEXAGON_HEAD_BOLT.CATPart
mechanical/ISO_4014_M4x40_STEEL_GRADE_A_HEXAGON_HEAD_BOLT.CATPart
mechanical/Motor-Base.CATPart
mechanical/Motor_Assy.CATProduct
mechanical/PCB.1.CATPart
mechanical/Reuleaux.CATPart
mechanical/asd.CATPart
mechanical/qwer.CATPart

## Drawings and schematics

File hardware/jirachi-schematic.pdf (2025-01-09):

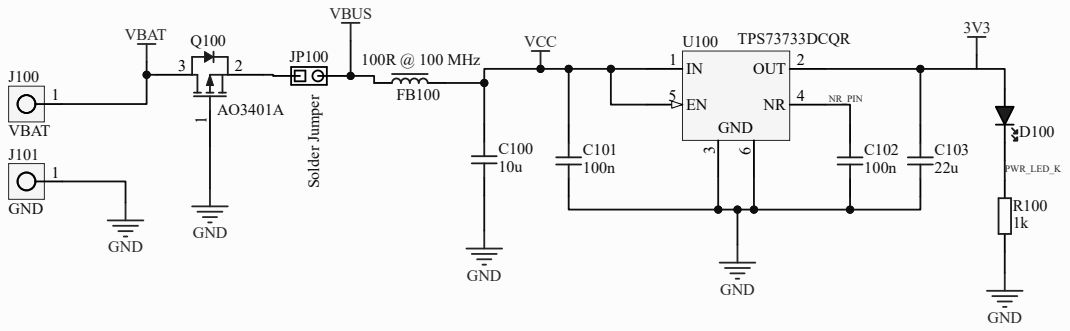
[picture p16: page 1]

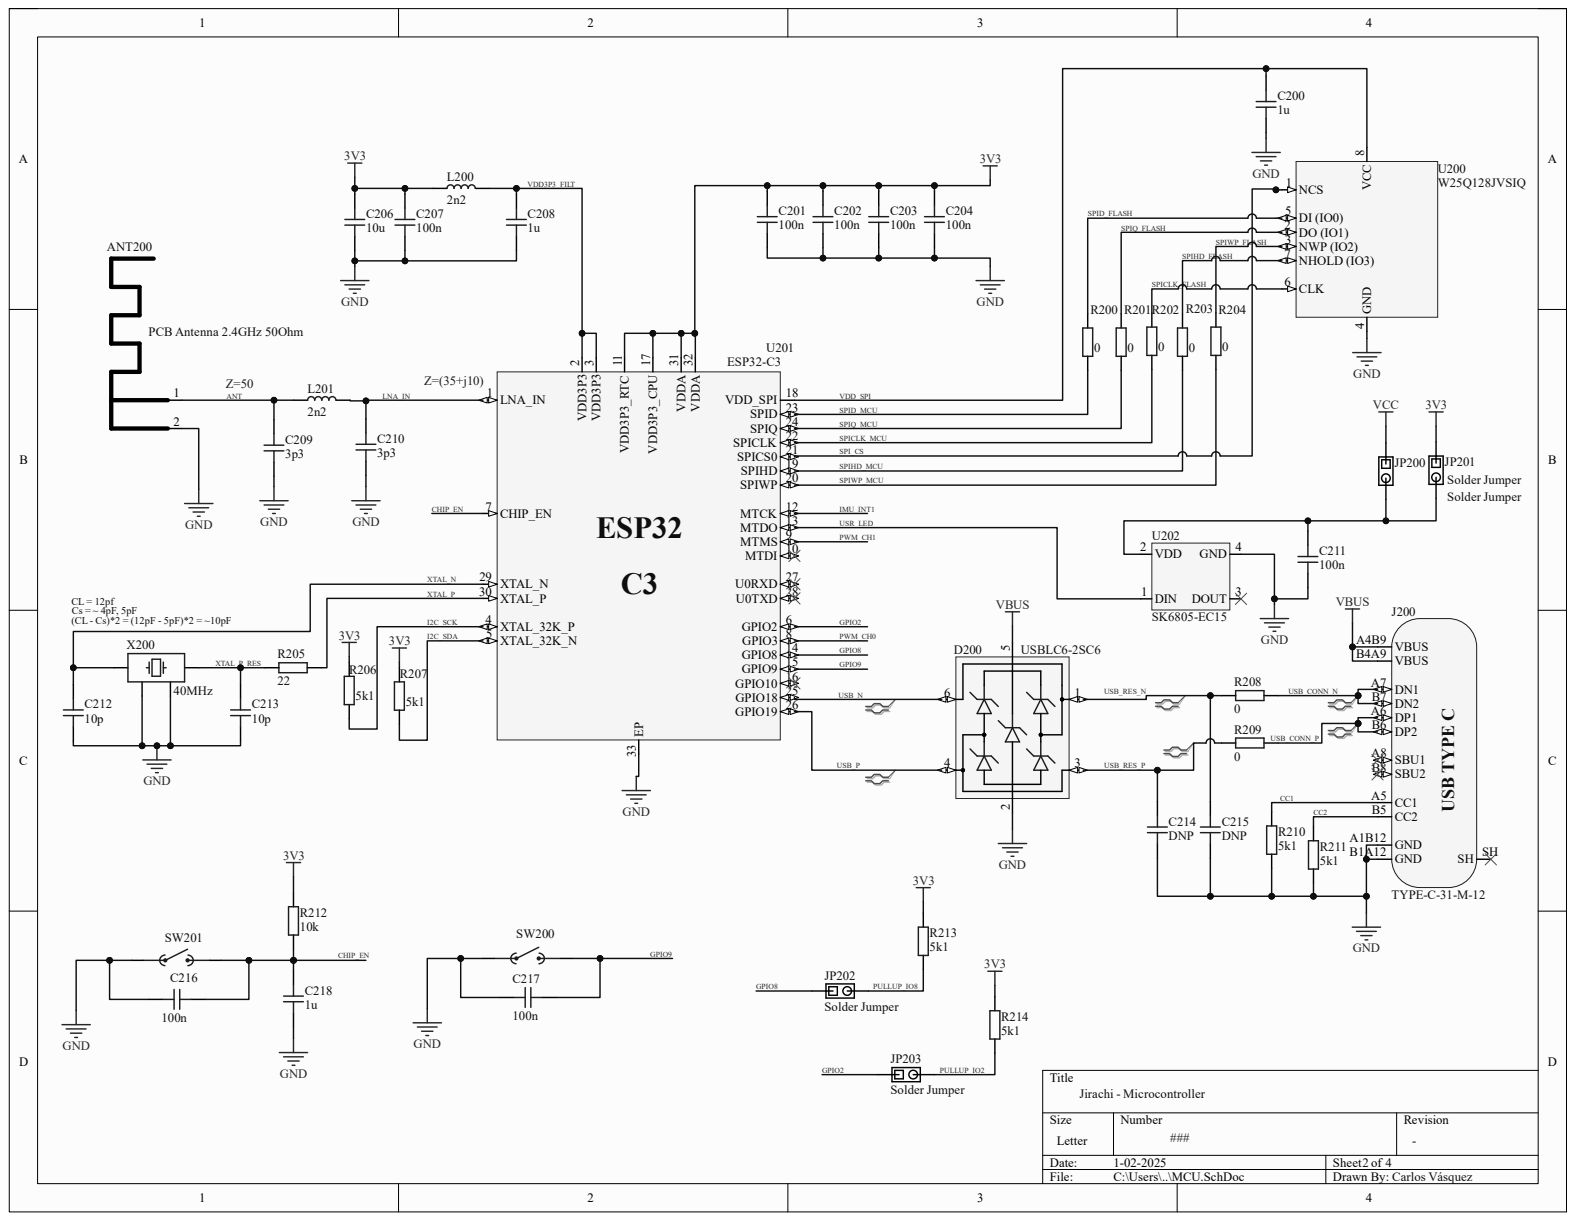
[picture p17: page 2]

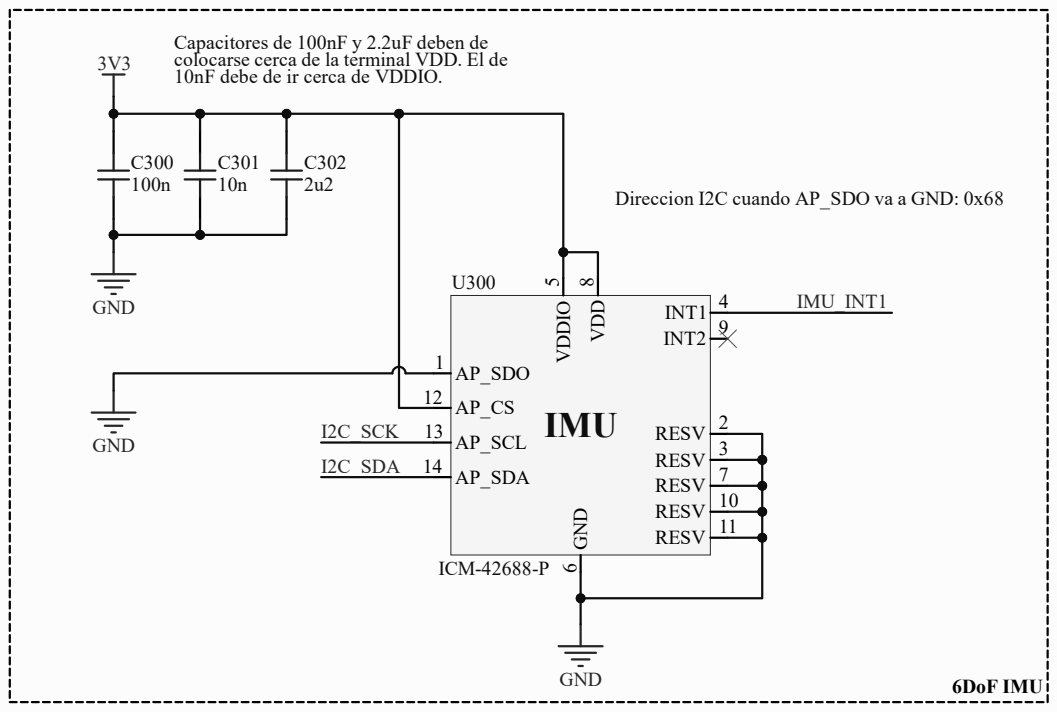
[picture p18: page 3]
Title; File:; C:\Users\..\Sensors.SchDoc; Drawn By: GND; 6 VDDIO; 5 VDD; RESV 2; RESV 10 RESV 11; RESV 3; INT1 4 INT2 9; AP_SCL 13; AP_SDO 1; AP_SDA 14; RESV 7; IMU; ICM-42688-P; GND; IMU_INT1; I2C_SCK; I2C_SDA; 6DoF IMU

Capacitores de 100nF y 2.2uF deben de
colocarse cerca de la terminal VDD. El de
10nF debe de ir cerca de VDDIO.

Direccion I2C cuando AP_SDO va a GND: 0x68

Jirachi - Inertial Measurement Unit

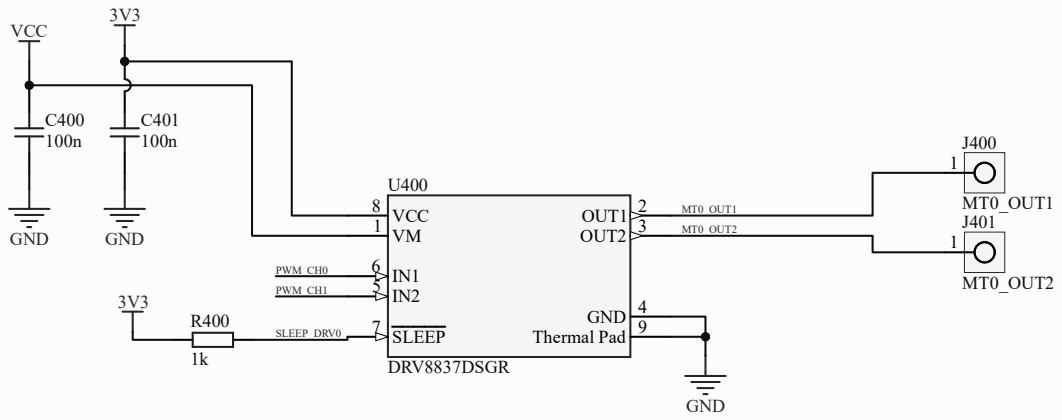
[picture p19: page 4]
Title; File:; C:\Users\..\Drivers.SchDoc; Drawn By:; VCC 8; OUT1 2; OUT2 3; SLEEP 7; Thermal Pad 9; GND 4; DRV8837DSGR; GND; VCC; PWM_CH1; PWM_CH0; MT0_OUT1; MT0_OUT2; SLEEP_DRV0

Jirachi - Motor Driver

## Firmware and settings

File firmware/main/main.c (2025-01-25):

/*
 * This file is part of the jirachi repository, https://github.com/gluonsandquarks/jirachi
 * main.c - main entry point. sets up the needed objects from the different apis, sets up
 * interrupts, calls to initialize peripherals, and overall functionality including the
 * main task which focuses on active control of the device
 * 
 * The MIT License (MIT)
 *
 * Copyright (c) 2025 gluons.
 *
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
 * THE SOFTWARE IS PROVIDED "AS IS", WITHOUT WARRANTY OF ANY KIND, EXPRESS OR
 * IMPLIED, INCLUDING BUT NOT LIMITED TO THE WARRANTIES OF MERCHANTABILITY,
 * FITNESS FOR A PARTICULAR PURPOSE AND NONINFRINGEMENT. IN NO EVENT SHALL THE
 * AUTHORS OR COPYRIGHT HOLDERS BE LIABLE FOR ANY CLAIM, DAMAGES OR OTHER
 * LIABILITY, WHETHER IN AN ACTION OF CONTRACT, TORT OR OTHERWISE, ARISING FROM,
 * OUT OF OR IN CONNECTION WITH THE SOFTWARE OR THE USE OR OTHER DEALINGS IN THE
 * SOFTWARE.
 */

#include "freertos/FreeRTOS.h"
#include "freertos/task.h"
#include "driver/gpio.h"
#include "esp_timer.h"
#include "esp_log.h"
#include <math.h>
#include <stdbool.h>
#include <stdio.h>
#include "globals.h"
#include "rgb.h"
#include "motor.h"
#include "imu.h"
#include "madgwick.h"
#include "pid.h"
#include "ble.h"

#define COLOR_SEQUENCE_SIZE      3U
#define PI                       (3.14159265358979F)
#define GYRO_MEASURE_ERROR       (PI * (40.0F / 180.0F))    /* this really should be measured, but estimated to 40deg/s -> omega_b on the original white paper */
                                                            /* technically this should be done by getting the mean bias of the gyro on every axis              */
                                                            /* ^ EDIT: since the original whitepaper has gotten more difficult to find, you can find a copy of */
                                                            /*         it inside the docs/ folder                                                              */
#define BETA(x)                  (sqrtf(3.0F / 4.0F) * (x)) /* compute beta for madgwick filter >w<!! */

#define DESIRED_ANGLE            (-60.0F)
#define DEFAULT_PID_KP           (3500.0F)
#define DEFAULT_PID_KD           (63.0F)
#define DEFAULT_PID_KI           (10.0F)
#define MAX_DUTY_CYCLE           (200U) /* full power!!!! :P */

volatile bool imu_data_ready = false;
volatile bool control_active = false;
volatile float pid_kp = DEFAULT_PID_KP;
volatile float pid_kd = DEFAULT_PID_KD;
volatile float pid_ki = DEFAULT_PID_KI;

static void IRAM_ATTR imu_isr_handler()
{
    gpio_intr_disable(IMU_INT1);
    gpio_isr_handler_remove(IMU_INT1);
    imu_data_ready = true;
    gpio_isr_handler_add(IMU_INT1, imu_isr_handler, NULL);
    gpio_intr_enable(IMU_INT1);
}

void app_main(void)
{

    /* sadly esp32c3 is single core so we need to do this in a different thread rather than a different core */
    /* might have some impact on active control?? need to stress test the app i guess */
    xTaskCreate((TaskFunction_t)ble_task, "ble_task", 4096, NULL, 1, NULL); /* start BLE task */

    /* set up color sequences for rgb led */
    RGB setup_state = { .hex = SUNSET_ORANGE };
    RGB control_sequence[COLOR_SEQUENCE_SIZE] = { { .hex = HOT_PINK },  { .hex = SORA_BLUE  }, { .hex = KUROMI_PURPLE } };
    RGB error_sequence[COLOR_SEQUENCE_SIZE]   = { { .hex = PLAIN_RED }, { .hex = SOSO_BLACK }, { .hex = PLAIN_RED     } };
    Morph morph = { 0 }; /* lightshow morph/blender manager for addressable LED */
    IMU imu = { 0 };
    Madgwick filter = { 0 };
    PID controller = { 0 };
    float control_signal = 0.0F;
    float deltat = 0.0F;
    int64_t now = 0.0F;
    uint8_t duty_cycle = 0U;

    pid_init(&controller, pid_kp, pid_kd, pid_ki);

    /* initialize peripherals */
    init_rmt();
    set_led_rgb(setup_state); /* init state */
    init_pwm();
    init_i2c();
    vTaskDelay(1000U / portTICK_PERIOD_MS);

    setup_state.hex = EVA_GREEN;
    set_led_rgb(setup_state); /* imu config state */

    /* check imu presence */
    uint8_t imu_id = imu_get_id();
    if (imu_id != ICM42688_ID)
    { 
        ESP_LOGE("main", "Critical error: IMU not connected or bad response. IMU_ID from response: 0x%X, should be 0x%X.", imu_id, ICM42688_ID);
        morph_set_sequence(&morph, error_sequence, COLOR_SEQUENCE_SIZE, 2000);
        while(1) { morph_tick(&morph); } /* show error sequence on led */
    }
    /* initialize imu struct + basic device config */
    imu_init(&imu, AFS_2G, GFS_500DPS, AODR_200Hz, GODR_200Hz, aMode_LN, gMode_LN, false);
    /* not necessary but helps with accuracy, the bias calculation can be commented out */
    ESP_LOGI("main", "CALCULATING ACCELEROMETER AND GYROSCOPE BIAS");
    ESP_LOGI("main", "KEEP DEVICE FLAT AND STABLE RELATIVE TO ONE AXIS ONLY");
    vTaskDelay(1000U / portTICK_PERIOD_MS);
    imu_calculate_bias(&imu);
    madgwick_init(&filter, BETA(GYRO_MEASURE_ERROR));

    /* configure IMU_INT1 pin for data ready interrupts coming from imu */
    gpio_reset_pin(IMU_INT1);
    gpio_set_direction(IMU_INT1, GPIO_MODE_INPUT);
    gpio_pullup_dis(IMU_INT1);
    gpio_pulldown_en(IMU_INT1);
    gpio_set_intr_type(IMU_INT1, GPIO_INTR_POSEDGE);
    gpio_install_isr_service(0U);
    gpio_isr_handler_add(IMU_INT1, imu_isr_handler, NULL);
    gpio_intr_enable(IMU_INT1);

    /* set lightshow to signal user control is active */
    morph_set_sequence(&morph, control_sequence, COLOR_SEQUENCE_SIZE, 2000);

    while (1)
    {
        if (imu_data_ready)
        {
            imu_data_ready = false;
            imu_read(&imu); /* INT1 cleared on any read BTW :p */
            now = esp_timer_get_time();
            deltat = ((float)(now - filter.last_update)) / 1000000.0F; /* calculate deltat and convert from us to s */
            filter.last_update = now;
            /* inputs flipped and fixed signs given the actual orientation of the imu on the board */
            madgwick_update(&filter, (imu.gy*PI/180.0F), (imu.gx*PI/180.0F), -(imu.gz*PI/180.0F), imu.ay, imu.ax, -imu.az, deltat);
        }
        madgwick_get_rpy(&filter);
        ESP_LOGD("main", "R: %03.2f,\tP: %03.2f,\tY: %03.2f", filter.roll, filter.pitch, filter.yaw);

        /* controller */
        /* pid control to make pitch = ~-60 degrees */
        if (control_active)
        {
            pid_update_consts(&controller, pid_kp, pid_kd, pid_ki); /* update constants from the BLE service */
            now = esp_timer_get_time();
            deltat = ((float)(now - controller.last_update)) / 1000000.0F;
            controller.last_update = now;
            control_signal = pid_compute(&controller, DESIRED_ANGLE, filter.pitch, deltat);
            ESP_LOGD("main", "control_signal = %f", control_signal);

            if (control_signal > 0.0F)
            {
                duty_cycle = (uint8_t)(control_signal > (float)MAX_DUTY_CYCLE ? MAX_DUTY_CYCLE : control_signal);
                set_motor_pwm(duty_cycle, 0U);
            }
            else
            {
                duty_cycle = (uint8_t)(-control_signal > (float)MAX_DUTY_CYCLE ? MAX_DUTY_CYCLE : -control_signal);
                set_motor_pwm(0U, duty_cycle);
            }
        } else { set_motor_pwm(0U, 0U); }

        
        morph_tick(&morph);
    }
}

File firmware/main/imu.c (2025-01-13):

/*
 * This file is part of the jirachi repository, https://github.com/gluonsandquarks/jirachi
 * imu.c - api and management of the inertial measurement unit onboard. i2c driver to initialize,
 * setup and custom config the imu, helper functions to get sensor readings, drift/bias estimation,
 * self-test, etc.
 * 
 * The MIT License (MIT)
 *
 * Copyright (c) 2025 gluons.
 *
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
 * THE SOFTWARE IS PROVIDED "AS IS", WITHOUT WARRANTY OF ANY KIND, EXPRESS OR
 * IMPLIED, INCLUDING BUT NOT LIMITED TO THE WARRANTIES OF MERCHANTABILITY,
 * FITNESS FOR A PARTICULAR PURPOSE AND NONINFRINGEMENT. IN NO EVENT SHALL THE
 * AUTHORS OR COPYRIGHT HOLDERS BE LIABLE FOR ANY CLAIM, DAMAGES OR OTHER
 * LIABILITY, WHETHER IN AN ACTION OF CONTRACT, TORT OR OTHERWISE, ARISING FROM,
 * OUT OF OR IN CONNECTION WITH THE SOFTWARE OR THE USE OR OTHER DEALINGS IN THE
 * SOFTWARE.
 */

#include <math.h>
#include "driver/i2c.h"
#include "esp_log.h"
#include "imu.h"

void init_i2c(void)
{
    i2c_port_t i2c_master_port = (i2c_port_t)I2C_PORT_NUM;
    i2c_config_t conf;
    conf.mode = I2C_MODE_MASTER;
    conf.sda_io_num = (gpio_num_t)I2C_MASTER_SDA_IO;
    conf.scl_io_num = (gpio_num_t)I2C_MASTER_SCL_IO;
    conf.sda_pullup_en = GPIO_PULLUP_ENABLE;
    conf.scl_pullup_en = GPIO_PULLUP_ENABLE;
    conf.master.clk_speed = I2C_MASTER_FREQ_HZ;
    conf.clk_flags = 0;

    esp_err_t err = i2c_param_config(i2c_master_port, &conf);
    if (err != ESP_OK) { ESP_LOGE("init_i2c", "I2C bus config failed: %d", err); }

    err = i2c_driver_install(i2c_master_port, conf.mode,
                             I2C_MASTER_RX_BUF_DISABLE,
                             I2C_MASTER_TX_BUF_DISABLE, 0);
    if (err != ESP_OK) { ESP_LOGE("init_i2c", "Failed to install I2C driver: %d", err); }
}

static void set_register(uint8_t register_address, uint8_t set_value)
{
    register_address = register_address & 0x007F; /* clamp address range from 0 - 127 */

    i2c_cmd_handle_t cmd = i2c_cmd_link_create();

    esp_err_t err = i2c_master_start(cmd);                                                    // send start bit
    if (err != ESP_OK) { ESP_LOGE("set_register", "i2c_master_start failed: %d", err); }

    err = i2c_master_write_byte(cmd, (ICM42688_ADDR << 1) | WRITE_BIT, ACK_CHECK_EN);         // IMU 7-bit address + write bit
    if (err != ESP_OK) { ESP_LOGE("set_register", "i2c_master_write_byte failed: %d", err); }

    err = i2c_master_write_byte(cmd, register_address, ACK_CHECK_EN);                         // target register
    if (err != ESP_OK) { ESP_LOGE("set_register", "i2c_master_write_byte failed: %d", err); }

    err = i2c_master_write_byte(cmd, set_value, ACK_CHECK_EN);                                // target value
    if (err != ESP_OK) { ESP_LOGE("set_register", "i2c_master_write_byte failed: %d", err); }

    err = i2c_master_stop(cmd);                                                               // send stop bit
    if (err != ESP_OK) { ESP_LOGE("set_register", "i2c_master_stop failed: %d", err); }

    err = i2c_master_cmd_begin((i2c_port_t)I2C_PORT_NUM, cmd, 1000U / portTICK_PERIOD_MS);     // send all queued commands
    if (err != ESP_OK) { ESP_LOGE("set_register", "i2c_master_cmd_begin failed: %d", err); }

    i2c_cmd_link_delete(cmd);
}

static uint8_t read_register(uint8_t register_address)
{
    uint8_t data = 0x00;
    register_address = register_address & 0x007F; /* clamp address range from 0 - 127 */

    i2c_cmd_handle_t cmd = i2c_cmd_link_create();

    esp_err_t err = i2c_master_start(cmd);                                                     // send start bit
    if (err != ESP_OK) { ESP_LOGE("read_register", "i2c_master_start failed: %d", err); }

    err = i2c_master_write_byte(cmd, (ICM42688_ADDR << 1) | WRITE_BIT, ACK_CHECK_EN);          // IMU 7-bit address + write bit
    if (err != ESP_OK) { ESP_LOGE("read_register", "i2c_master_write_byte failed: %d", err); }

    err = i2c_master_write_byte(cmd, register_address, ACK_CHECK_EN);                          // register to be read
    if (err != ESP_OK) { ESP_LOGE("read_register", "i2c_master_write_byte failed: %d", err); }

    err = i2c_master_start(cmd);                                                               // resend start bit
    if (err != ESP_OK) { ESP_LOGE("read_register", "i2c_master_start failed: %d", err); }

    err = i2c_master_write_byte(cmd, (ICM42688_ADDR << 1) | READ_BIT, ACK_CHECK_EN);           // IMU 7-bit address + read bit
    if (err != ESP_OK) { ESP_LOGE("read_register", "i2c_master_write_byte failed: %d", err); }

    err = i2c_master_read_byte(cmd, &data, I2C_MASTER_NACK);                                   // read into data buffer
    if (err != ESP_OK) { ESP_LOGE("read_register", "i2c_master_read_byte failed: %d", err); }

    err = i2c_master_stop(cmd);                                                                // send stop bit
    if (err != ESP_OK) { ESP_LOGE("read_register", "i2c_master_stop failed: %d", err); }

    err = i2c_master_cmd_begin((i2c_port_t)I2C_PORT_NUM, cmd, 1000U / portTICK_PERIOD_MS);      // send all queued commands
    if (err != ESP_OK) { ESP_LOGE("read_register", "i2c_master_cmd_begin failed: %d", err); }

    i2c_cmd_link_delete(cmd);

    return data;
}

static void set_accel_resolution(IMU *imu, uint8_t scale)
{
    switch(scale)
    {
        case AFS_2G:
            imu->accel_resolution = 2.0F / 32768.0F;
            break;
        case AFS_4G:
            imu->accel_resolution = 4.0F / 32768.0F;
            break;
        case AFS_8G:
            imu->accel_resolution = 8.0F / 32768.0F;
            break;
        case AFS_16G:
            imu->accel_resolution = 16.0F / 32768.0F;
            break;
    }
}

static void set_gyro_resolution(IMU *imu, uint8_t scale)
{
    switch(scale)
    {
        case GFS_15_625DPS:
            imu->gyro_resolution = 15.625F / 32768.0F;
            break;
        case GFS_31_25DPS:
            imu->gyro_resolution = 31.25F / 32768.0F;
            break;
        case GFS_62_50DPS:
            imu->gyro_resolution = 62.5F / 32768.0F;
            break;
        case GFS_125DPS:
            imu->gyro_resolution = 125.0F / 32768.0F;
            break;
        case GFS_250DPS:
            imu->gyro_resolution = 250.0F / 32768.0F;
            break;
        case GFS_500DPS:
            imu->gyro_resolution = 500.0F / 32768.0F;
            break;
        case GFS_1000DPS:
            imu->gyro_resolution = 1000.0F / 32768.0F;
            break;
        case GFS_2000DPS:
            imu->gyro_resolution = 2000.0F / 32768.0F;
            break;
    }
}
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

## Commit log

2025-01-10 fixed deltat calculation, removed extra code from madgwick.c, added wait periods on imu initialization, minor code changes
    [imu.c, main.c, motor.h]
2025-01-12 added ble support, ability to control device from ble client, parser for ble incoming data, cleaned up the different translation units
2025-01-13 added multiple ble characteristics to fully control the pid controller, basic data parser refactor, documentation, a little refactoring here and there i think lol
2025-01-13 changed ble device name, fixed implicit cast minor warning on main
    [main.c]
2025-01-14 scrapped the webpage idea, too horrible to be crossplatform and ble needs on windows too tiring for a personal project, switching to linux and rust for some control gui
2025-01-21 started working on desktop app to control the device through BLE
2025-01-23 added extra logic to gui, loading screen, fixed the scanned device list, etc...
    [main.rs]
2025-01-23 added controls to control screen for the different constants on the connected device
2025-01-23 implemented basic PoC to scan for BLE peripherals under the iced framework
2025-01-25 implemented async function to connect to the selected peripheral and returned the peripheral obj on success or error if peripheral hella sus
    [main.rs]
2025-01-25 fetching data from the device is now possible, reflected on the gui too!!!
2025-01-27 added mechanical and hardware files
    [10.CATPart, 11.CATPart, 3.CATPart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]
2025-01-27 added documentation to hardware and mechanical
    [Lucido.PcbDoc]
2025-01-29 added bom to hardware readme
2025-02-12 finished mechanical design, added documentation to the mechanical folder, addded missing bom elements
    [10.CATPart, 11.CATPart, 18650.CATPart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]
2025-02-12 added missing bom elements
2025-02-12 added link to bom
